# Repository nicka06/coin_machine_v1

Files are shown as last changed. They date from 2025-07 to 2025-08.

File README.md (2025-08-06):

# coin_machine_v1

This is an automated coin machine, allowing an individual to easily take pictures of all the coins that they have. It works very simply. The user inserts the coin into the chute located at the front of the machine. Once the coin has made its way to the flipper, the servo flips it over twice, allowing the camera to take a picture of both sides. Following the completion of the flips, the coin is ejected, taking it through external coin chute and collection box. Beyond the mechanics of the camera/flipper system, the system has an additional chute that is opened by the servo connected to the excursion on the right side of the mahine. If the system recognizes multiple coins in the system (via the phototransistor sensor), the chute will open up, removing the extra coins from the system via the second external coin chute. This coin chute brings the extra coins to the front of the machine.

I'm building this automated coin machine due to my love of coins. I enjoy collecting them and taking pictures of the new ones I get at the bank to keep track of them. As you can imagine, this is an extremely difficult and annoying process. This cuts through all of it, making the grueling process much better. Later, I'll also be able to add more features such as automatic value estimator and more. I can't wait to finish building it!
Screenshot 2025-08-06 at 12 46 12 AM
Front chute
Screenshot 2025-08-06 at 12 53 51 AM

Screenshot 2025-07-26 at 3 54 14 PM

|Item |Link |Step/STL File |Price (bf tax + ship)|Quantity|Total |
|---|---|---|---|---|---|
|Microcontroller |https://www.digikey.com/en/products/detail/espressif-systems/ESP32-DEVKITC-32E/12091810?gQT=2 |N/A |8.09 |1 |16.18 |
|Battery Holder |https://www.digikey.com/en/products/detail/olimex-ltd/BAT-HOLDER-4XAA/21662650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 |DNE |0.59 |1 |1.18  |
|Servos |https://www.amazon.com/Miuzei-Geared-Helicopter-Arduino-Project/dp/B0CP98TZJ2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 |https://www.electronicoscaldas.com/datasheet/MG90S_Tower-Pro.pdf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 |13.99 |0.5 |13.99 |
|Sensor |https://www.digikey.com/en/products/detail/lite-on-inc/LTH-301-05/3198344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 |https://optoelectronics.liteon.com/upload/download/DS-55-92-0002/H301-05.pdf |0.7 |1 |1.4 |
|Light indicator |https://www.digikey.com/en/products/detail/inolux/HV-5RGB60/7604616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 |https://www.inolux-corp.com/datasheet/Inolux%20Lamp/TH%20Lamp/HV-5RGBXX%205mm%20Full-Color%20Series.pdf |1.06 |1 |2.12  |
|Camera |https://www.alibaba.com/product-detail/p_62408774762.html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 |https://us-icbuim-file.oss-us-east-1.aliyuncs.com/chat/bdf5eb8cdbcff22f275396a9d335c13d.pdf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|1.92 |1 |3.84  |
|Camera lights |https://www.amazon.com/BTF-LIGHTING-WS2812B1M60LB30-BTF-LIGHTING-WS2812B-IC-RGB-5050SMD-Pure-Gold-Individual-Addressable-LED-Strip-High-Quality-3-28FT-60LED-60LED-m-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 |DNE |8.99 |0.5 |8.99  |
|buck converter |https://www.alibaba.com/product-detail/p_1601286665356.html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 |DNE |0.38 |1 |0.76  |
|1000Uf Capacitor |https://www.digikey.com/en/products/detail/nichicon/UCM1C102MNL1GS/4991837 |N/A |1.03 |1 |2.06  |
|indicator resistor  |https://www.digikey.com/en/products/detail/yageo/RC0805FR-10220RL/14008826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 |N/A |0.1 |1 |0.2 |
|ligihting resistor  |https://www.digikey.com/en/products/detail/yageo/RC0805FR-13470RL/14287677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 |N/A |0.1 |3 |0.6 |
|Power Connector |https://www.digikey.com/en/products/detail/w-rth-elektronik/691137710002/6644051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 |N/A |0.74 |1 |1.48  |
|Servo connector |https://www.digikey.com/en/products/detail/w-rth-elektronik/61300311121/4846825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 |N/A |0.12 |2 |0.48  |
|Sensor board male |https://www.digikey.com/en/products/detail/jst-sales-america-inc/B4B-XH-A/1651047 |N/A |0.14 |1 |0.28  |
|Sensor female |https://www.digikey.com/en/products/detail/jst-sales-america-inc/XHP-4/683353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 |N/A |0.1 |1 |0.2 |
|Sensor Connector |https://www.digikey.com/en/products/detail/jst-sales-america-inc/ASXHSXH22K254/9961919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 |N/A |0.77 |4 |6.16  |
|Indicator board male|https://www.digikey.com/en/products/detail/jst-sales-america-inc/B4B-XH-A/1651047 |N/A |0.14 |1 |0.28  |
|Indicator Female |https://www.digikey.com/en/products/detail/jst-sales-america-inc/XHP-4/683353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 |N/A |0.1 |1 |0.2 |
|Indicator Connector |https://www.digikey.com/en/products/detail/jst-sales-america-inc/ASXHSXH22K254/9961919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 |N/A |0.77 |4 |6.16  |
|Lightning Board Male|https://www.digikey.com/en/products/detail/jst-sales-america-inc/B3B-XH-A/1651046?gQT=2 |N/A |0.11 |1 |0.22  |
|Lightning Female |https://www.digikey.com/en/products/detail/jst-sales-america-inc/XHP-3/1651017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 |N/A |0.1 |1 |0.2 |
|Lightning Connector |https://www.digikey.com/en/products/detail/jst-sales-america-inc/ASXHSXH22K102/9961917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 |N/A |0.71 |3 |4.26  |
|Camera Connector |https://www.digikey.com/en/products/detail/gct/FFC2B35-24-T/15970899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 |N/A |0.44 |1 |0.88  |
|Camera Wire |https://www.digikey.com/en/products/detail/gct/05-24-D-0101-A-4-06-4-T/21266768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 |N/A |1.29 |1 |2.58  |
|Regular wire |https://www.amazon.com/Fermerry-Stranded-Electrical-Silicone-Cables/dp/B089CHVN7G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 |N/A |9.99 |0.5 |9.99  |
|Foam for pcb |https://www.aliexpress.us/item/3256805442378894.html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 |N/A |6.58 |0.5 |6.58  |
|Screws |https://www.homedepot.com/p/Everbilt-M3-0-5-x-10-mm-Plain-Metric-Socket-Cap-Screw-3-Piece-per-Bag-803188/204808024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 |N/A |2.25 |2 |9 |
|More Screws |https://www.homedepot.com/p/Prime-Line-M2-0-4-x-20-mm-Black-Oxide-Coated-Steel-Class-12-9-Metric-Internal-Hex-Socket-Head-Set-Screws-10-Pack-9180136/311732337 |N/A |4.99 |0.5 |4.99  |
|Magnets |https://www.aliexpress.us/item/3256807909032358.html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|N/A |0.99 |1 |1.98  |
|filament |https://www.amazon.com/eSUN-Filament-Printing-Printer-Designed/dp/B0DGQBMJMK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 |N/A |13.39 |0.5 |13.39 |
|pcb |N/A |N/A |2 |0.5 |2 |
|Shipping + Tax | | | | |35 |
| | | | | |157.63|
| | |a | | | |

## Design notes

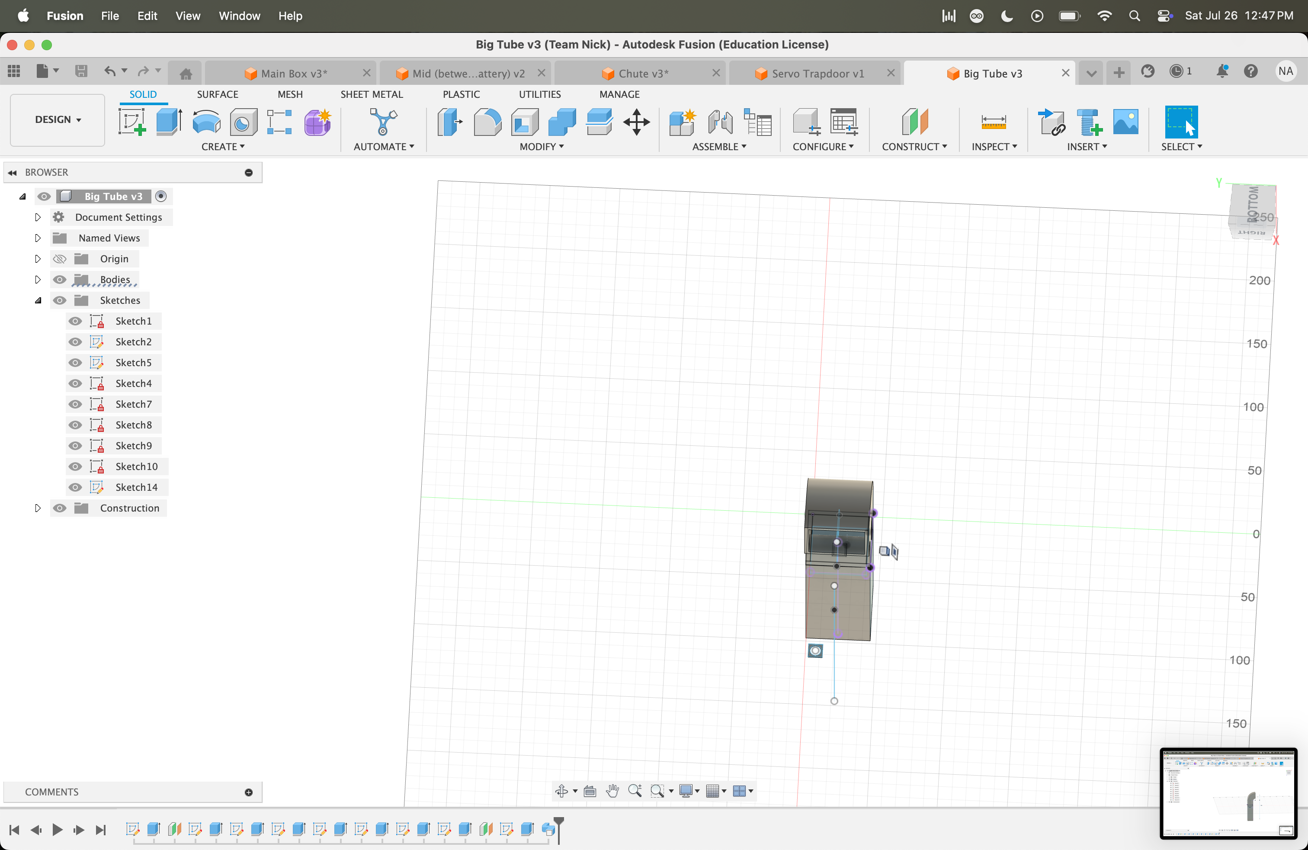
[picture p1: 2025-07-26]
pics/Screenshot 2025-07-26 at 12.47.22 PM.png

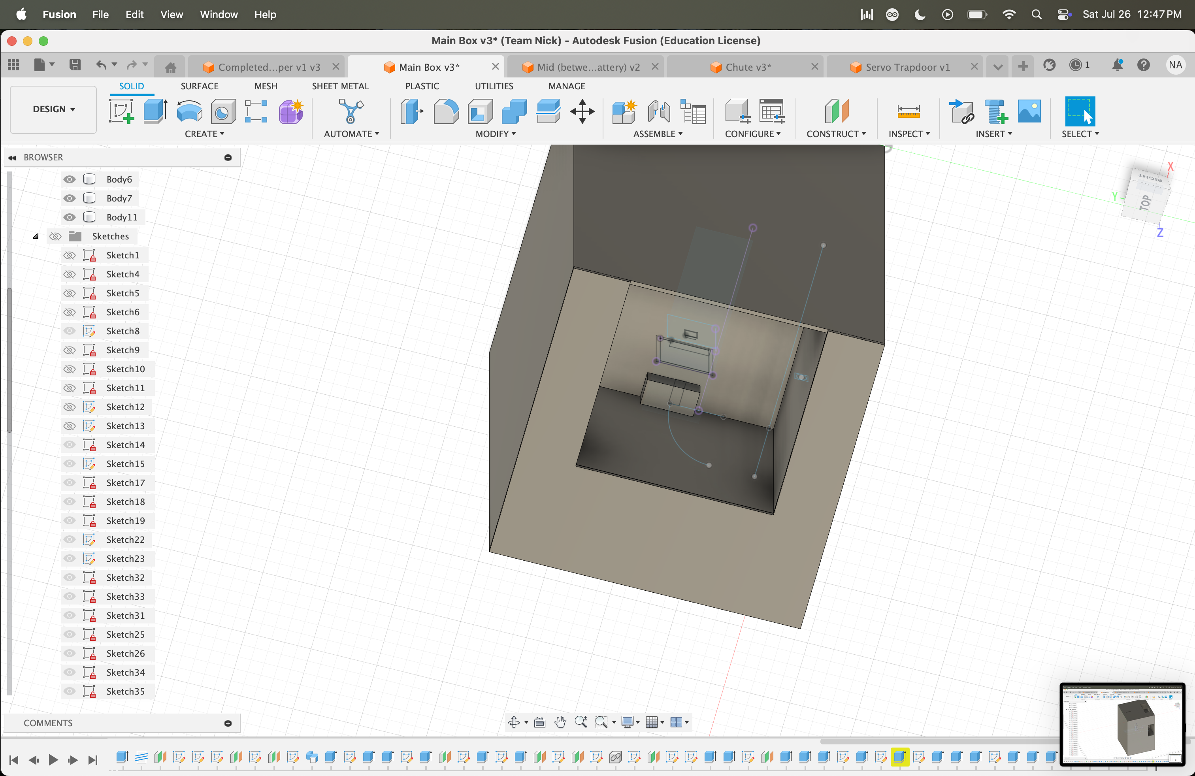
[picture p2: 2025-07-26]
pics/Screenshot 2025-07-26 at 12.47.51 PM.png

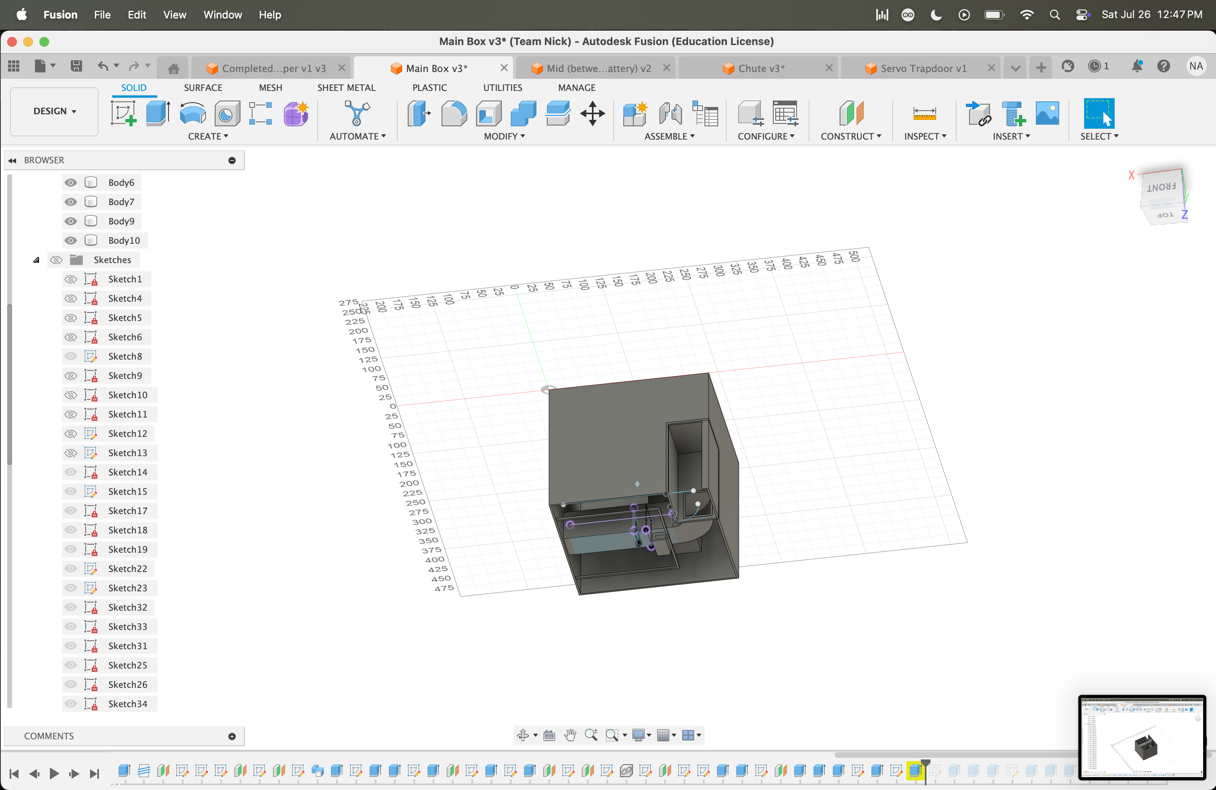
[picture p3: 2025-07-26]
pics/Screenshot 2025-07-26 at 12.47.39 PM.png

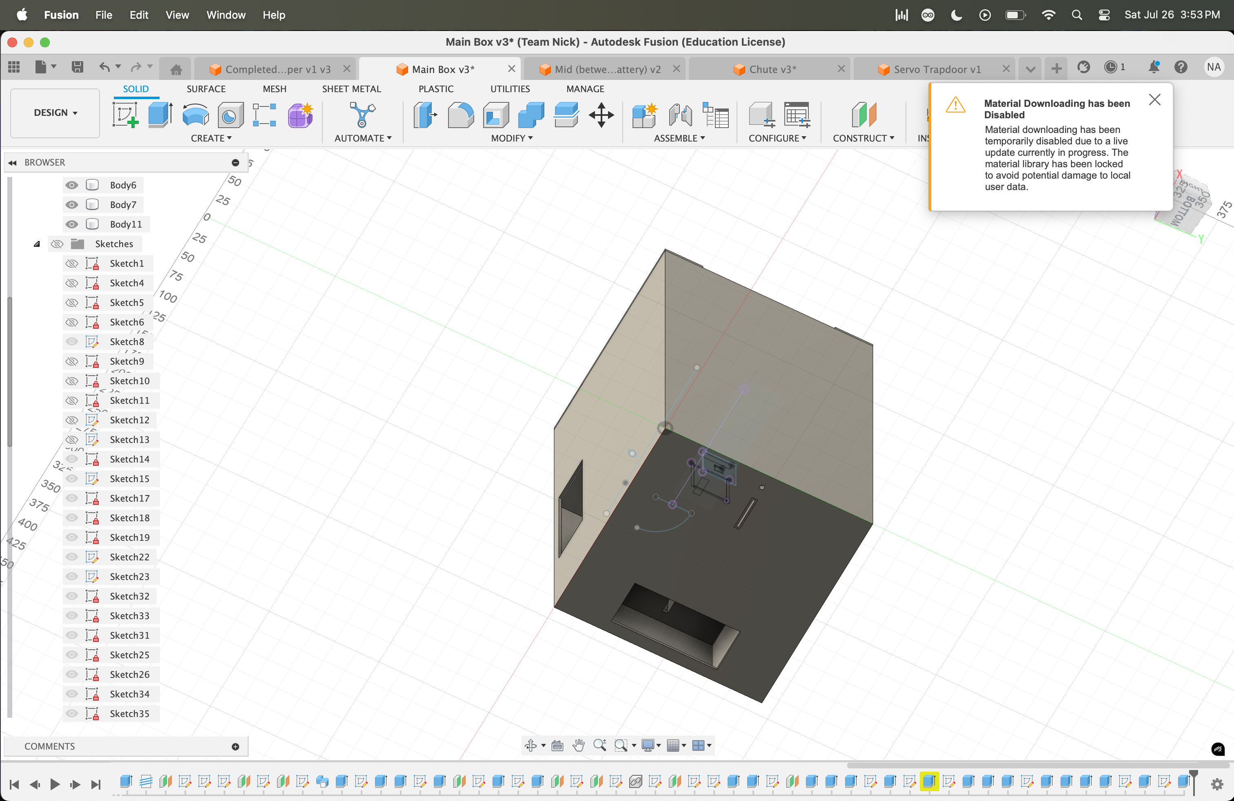
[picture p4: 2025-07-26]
pics/Screenshot 2025-07-26 at 3.53.41 PM.png

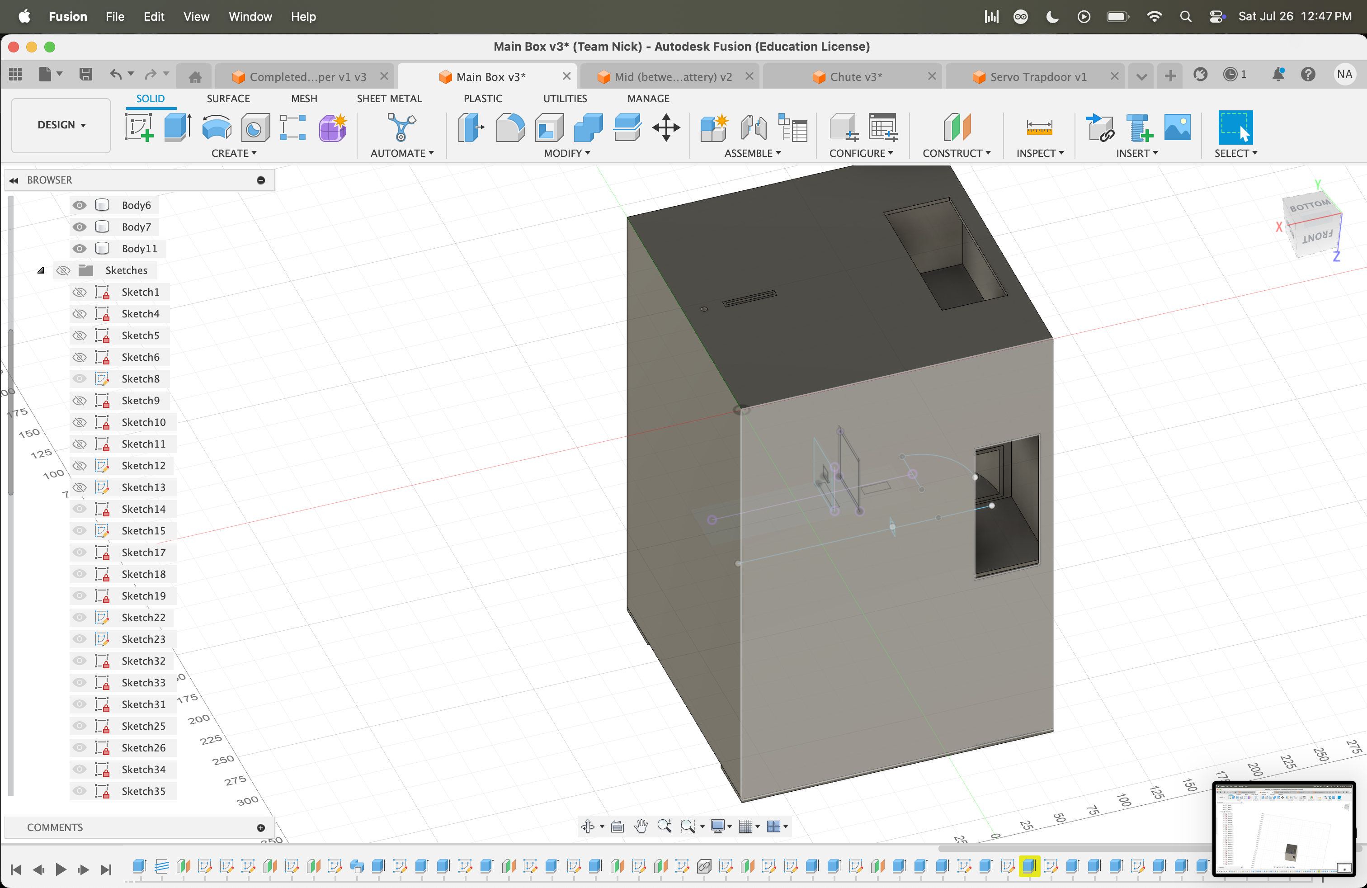
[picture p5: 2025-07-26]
pics/Screenshot 2025-07-26 at 12.47.49 PM.png

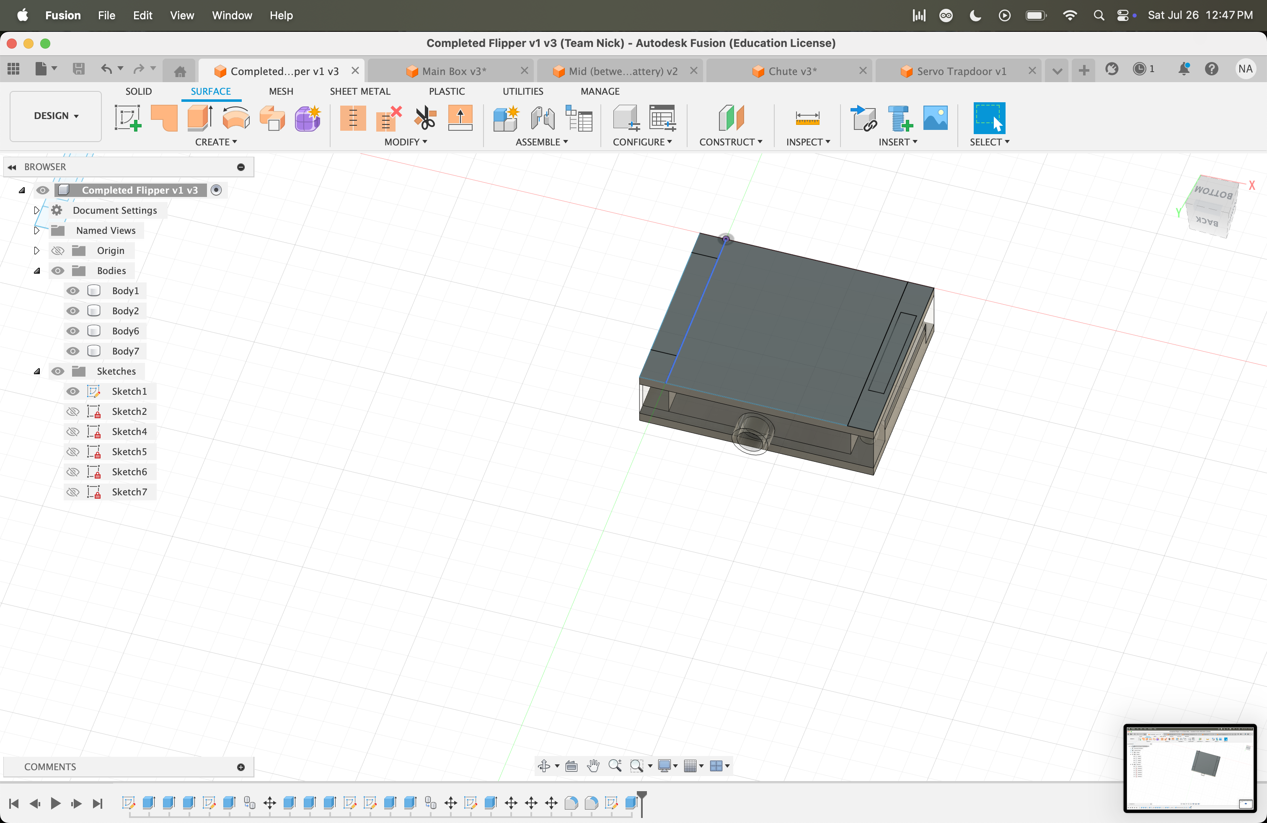
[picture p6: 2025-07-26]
pics/Screenshot 2025-07-26 at 12.47.08 PM.png

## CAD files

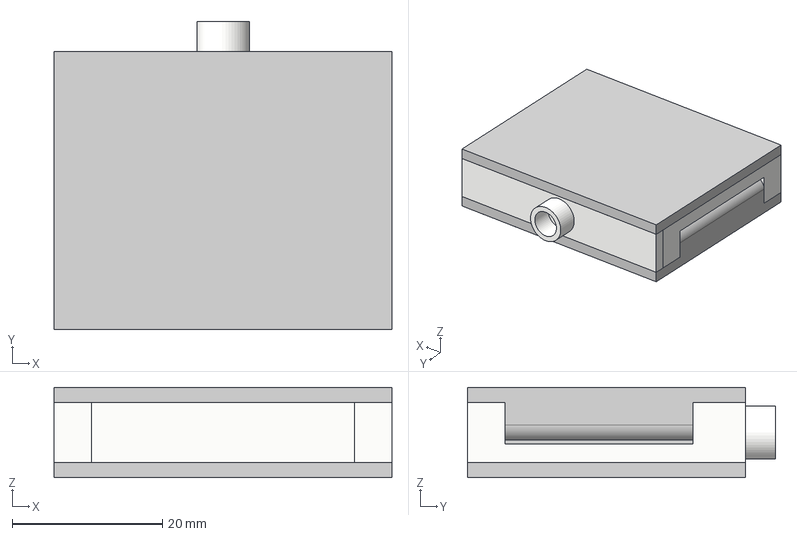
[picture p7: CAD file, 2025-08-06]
cad/Completed Flipper v1 v3.step
45.0 x 41.0 x 12.0 mm

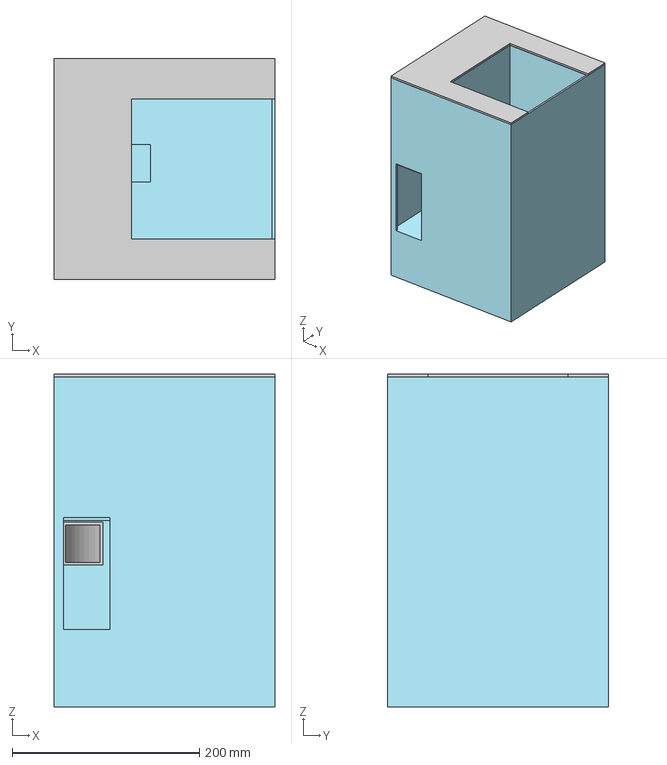
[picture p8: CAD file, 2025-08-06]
cad/Main Box v6.step
236.2 x 236.2 x 356.0 mm
Big Tube
Chute

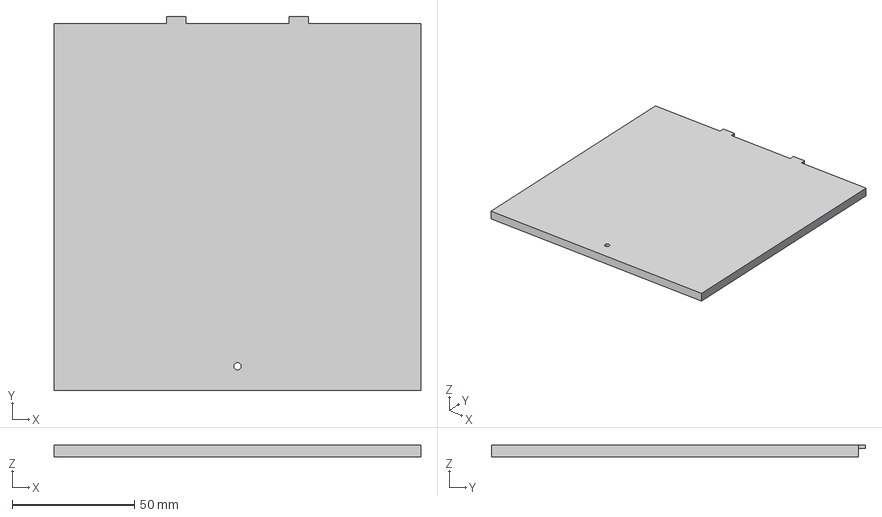
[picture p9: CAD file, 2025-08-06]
cad/Back Side v2.step
150.0 x 153.0 x 5.00 mm

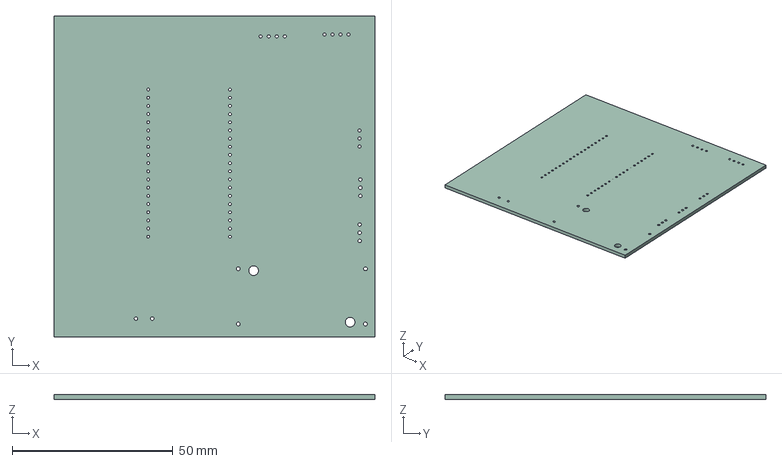
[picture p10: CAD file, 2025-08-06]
cad/Automated Coin Machine v1.step
99.6 x 99.7 x 1.51 mm

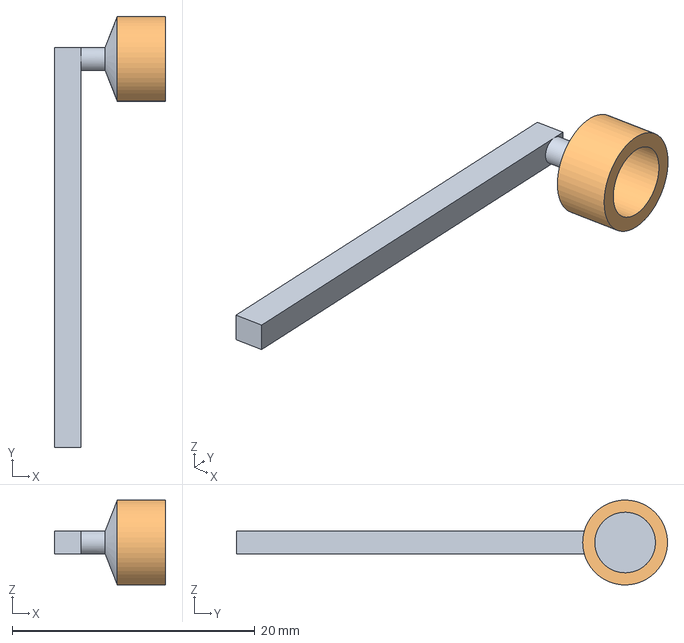
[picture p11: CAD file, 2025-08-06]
cad/Servo Trapdoor v1.step
9.19 x 35.5 x 7.00 mm

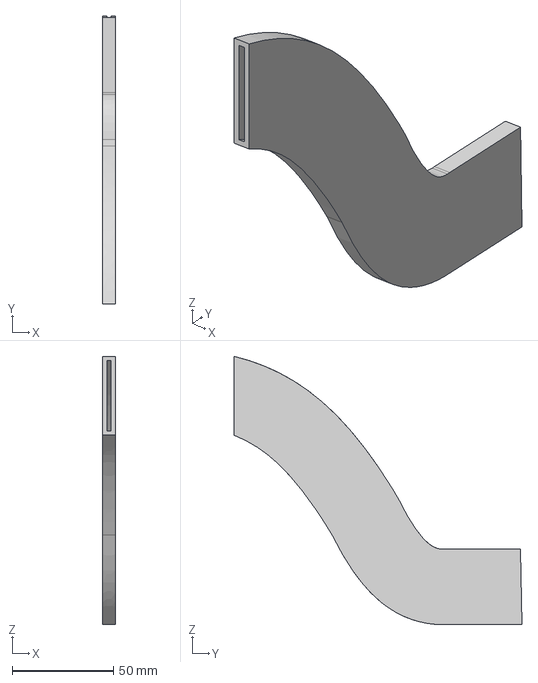
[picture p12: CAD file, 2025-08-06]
cad/Chute v4.step
6.20 x 142.4 x 132.6 mm

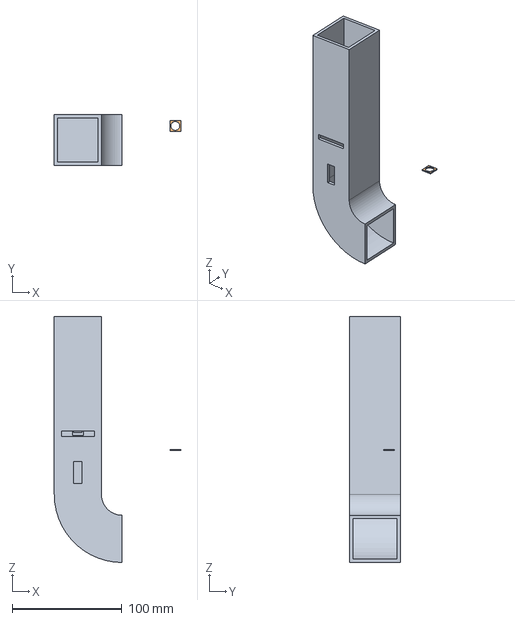
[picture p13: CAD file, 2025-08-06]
cad/Big Tube v3.step
115.2 x 46.0 x 224.0 mm

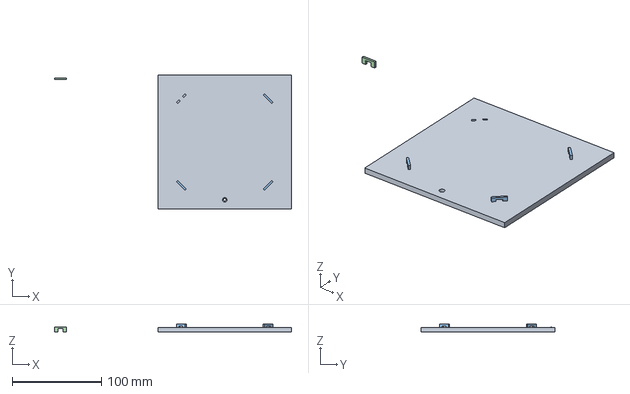
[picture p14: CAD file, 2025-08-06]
cad/PCB Plate v2.step
266.3 x 150.0 x 8.80 mm

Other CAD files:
cad/Main Box v4.stl
cad/Mid (between pcb and battery) v2.step
cad/Back Side v2.stl
cad/Big Tube v3.stl
cad/Chute v4.stl
cad/Completed Flipper v1 v3.stl
cad/Mid (between pcb and battery) v2.stl
cad/PCB Plate v2.stl
cad/Servo Trapdoor v1.stl

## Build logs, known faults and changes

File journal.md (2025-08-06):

---
title: Automated Coin Machine
author: Nick
description: Automates Coin Recognition
created_at: "2024-07-20"
---

Total Time Spent ~ 20 hrs

7/20/2025 -- 1.5 hours

Forgot to update this yesterday but I'll go ahead and do this now. I started to work on the cad for the actual flipper that will open up and allow the coins to take the images. It essentially works by having two magnets that hold it shut when it's not being pried open by the bar in the main rectangular tube. These act as the bottoms so the coin doens't fall down the chute prematurely. The actual "cading" wasn't too hard but I had to go back several times to make adjustments on the sizing. I also sketched out the rest of the box and started to create a bom. I'll attach an image of the sketches that I made yesterday


7/21/2025 --3 hours

Continued to build out the chute on the cad as well as the bom. The bill of materials has been harder than I originally thought as finding the correct parts and then making sure that the schematic and 3d orientation will work correctly all togethor is nothing short of a pain in the butt. Additionally, when building out the chute, I couldn't figure out how to get it to go along on the path that I wanted it to go on. I looked it up on chat gpt, google, reddit, etc and nothing worked. Eventually, I just created it using the sweep and then extruded a cut so that the one end would be flat 90 degrees but there has to be a better way of going about that. 
Screenshot 2025-07-22 at 11 32 43 PM
Screenshot 2025-07-22 at 11 33 04 PM

7/22/2025 -4 hours

Created all of the symbols and built out the schematic. This was a HUGE pain in the butt, but kinda fun at the same time. The good news is that it sort of paid off to go through all the bill of materials was correct the first time. I had to consult with chat gpt and google a lot when building out most of the schematic as I'm fairly novice in this work. In terms of efficiency, I feel like 4-5 hours for working on a schematic isn't that bad especially for someone who hasn't done it a ton like me. 

Screenshot 2025-07-22 at 11 34 23 PM

Screenshot 2025-07-23 at 1 27 12 PM
Screenshot 2025-07-23 at 1 27 17 PM

7/24/2025 - 5 hrs

Started to build out the actual box and rest of the components via fusion360 to finish up the project. This should have gone a lot easier then it did. Despite the fact that I had all the pieces with the correct heights and dimensions on them, the pieces were still really finnecky when going into place. Eventually, I looked up a manual for fusion 3690 and realized that you can do point to point connections which turned out to be a life saver. Will finish the rest of the cad by tomorrow. 

7/25/2025 - 1 HR

Again, I continue to work on the project. Today, I had a huge setback as I realized the chute ran into the servo. WHAT A PAIN. So, I took some time to extrude another 3.6 millimaters to the end of the chute and then extended the rest of the infastructure (flipper, main rectangular thing, side exterior coin holder, etc) so that all of that would work with the new dimensions that i worked with.
7/26/2025 - 4 hrs

Finished everyhting up!!! The final github uploads and downloading all the content wasn't a whole lot of fund but Ican feel how ready I am to start building it out!

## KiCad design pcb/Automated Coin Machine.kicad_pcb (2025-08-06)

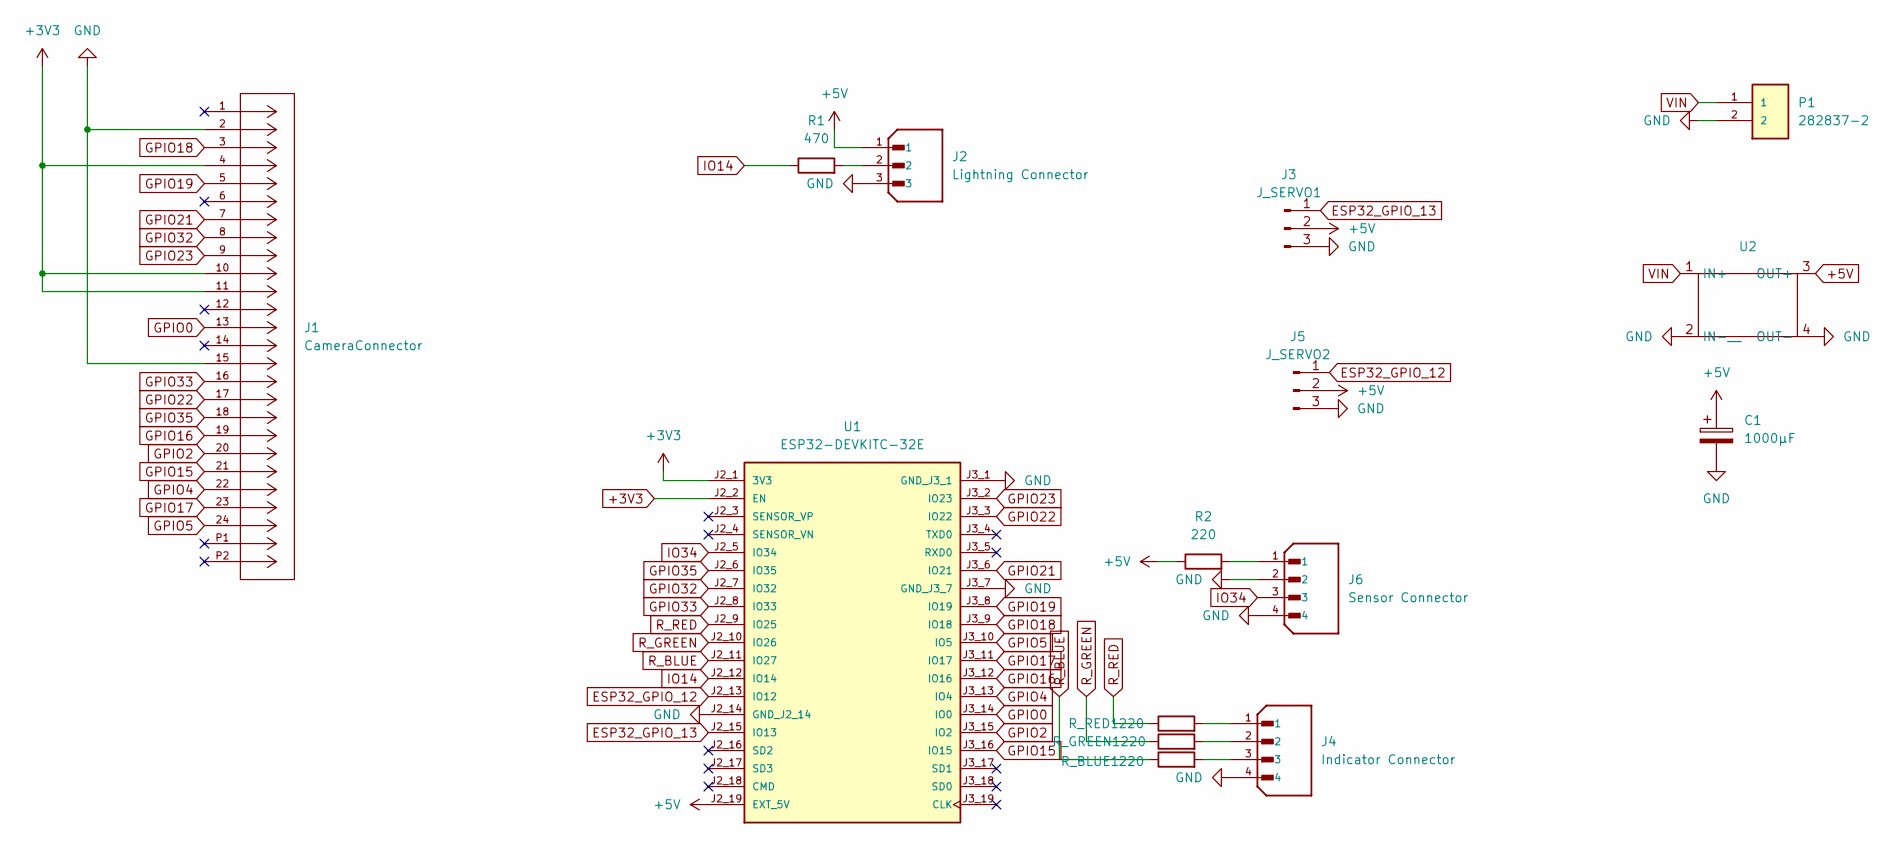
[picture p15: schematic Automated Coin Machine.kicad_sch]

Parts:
C1: 1000µF; 1000UFCapacitor
J1: CameraConnector; MANUFACTURER_PART_NUMBER 5051102491
J2: Lightning Connector; LightningConnector; PARTREV 7/4/21; DigiKey_Part_Number 455-2248-ND
J3: J_SERVO1; ServoConnector
J4: Indicator Connector; SensorIndicatorConnector; PARTREV 7/4/21; DigiKey_Part_Number 455-B4B-XH-A-ND
J5: J_SERVO2; ServoConnector
J6: Sensor Connector; SensorIndicatorConnector; PARTREV 7/4/21; DigiKey_Part_Number 455-B4B-XH-A-ND
P1: 282837-2; PowerConnector; PARTREV G3
R1: 470; LightningResistor
R2: 220; IndicatorResistor
R_BLUE1: 220; IndicatorResistor
R_GREEN1: 220; IndicatorResistor
R_RED1: 220; IndicatorResistor
U1: ESP32-DEVKITC-32E; ESP32; PARTREV 1.4
U2: LM2596_Module

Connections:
+3V3: J1.4, J1.10, J1.11, U1.J2_1 (3V3), U1.J2_2 (EN)
+5V: C1.1, J2.1, J3.2, J5.2, R2.1, U1.J2_19 (EXT_5V), U2.3 (OUT+)
ESP32_GPIO_12: J5.1, U1.J2_13 (IO12)
ESP32_GPIO_13: J3.1, U1.J2_15 (IO13)
GND: C1.2, J1.2, J1.15, J2.3, J3.3, J4.4, J5.3, J6.2, J6.4, P1.2, U1.J2_14 (GND_J2_14), U1.J3_1 (GND_J3_1), U1.J3_7 (GND_J3_7), U2.2 (IN-__), U2.4 (OUT-)
GPIO0: J1.13, U1.J3_14 (IO0)
GPIO2: J1.20, U1.J3_15 (IO2)
GPIO4: J1.22, U1.J3_13 (IO4)
GPIO5: J1.24, U1.J3_10 (IO5)
GPIO15: J1.21, U1.J3_16 (IO15)
GPIO16: J1.19, U1.J3_12 (IO16)
GPIO17: J1.23, U1.J3_11 (IO17)
GPIO18: J1.3, U1.J3_9 (IO18)
GPIO19: J1.5, U1.J3_8 (IO19)
GPIO21: J1.7, U1.J3_6 (IO21)
GPIO22: J1.17, U1.J3_3 (IO22)
GPIO23: J1.9, U1.J3_2 (IO23)
GPIO32: J1.8, U1.J2_7 (IO32)
GPIO33: J1.16, U1.J2_8 (IO33)
GPIO35: J1.18, U1.J2_6 (IO35)
IO14: R1.1, U1.J2_12 (IO14)
IO34: J6.3, U1.J2_5 (IO34)
unnamed: J2.2, R1.2
unnamed: J4.1, R_RED1.2
unnamed: J4.2, R_GREEN1.2
unnamed: J4.3, R_BLUE1.2
unnamed: J6.1, R2.2
R_BLUE: R_BLUE1.1, U1.J2_11 (IO27)
R_GREEN: R_GREEN1.1, U1.J2_10 (IO26)
R_RED: R_RED1.1, U1.J2_9 (IO25)
VIN: P1.1, U2.1 (IN+)

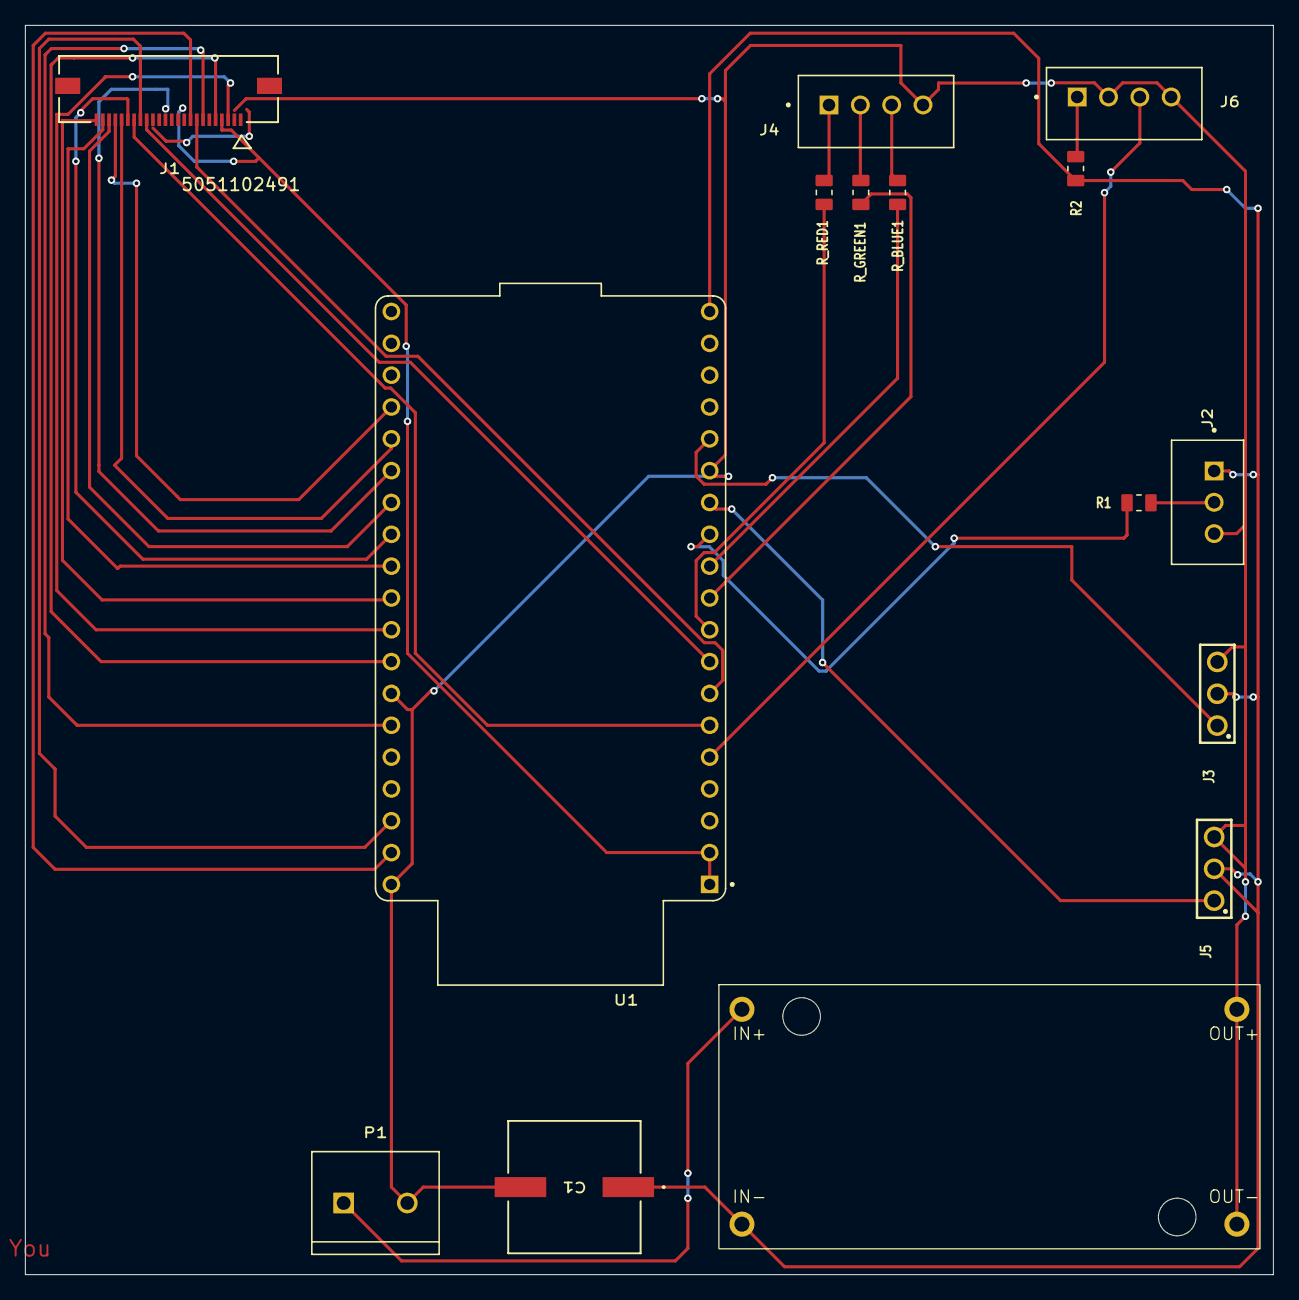
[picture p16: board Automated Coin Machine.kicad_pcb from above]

Board: 2 copper layers, 99.6 x 99.7 mm, 15 parts (0 on the bottom side), 31 nets.

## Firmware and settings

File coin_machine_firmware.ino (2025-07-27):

/*
 * Automated Coin Machine Firmware
 * ESP32 Arduino Code
 * 
 * This firmware controls an automated coin recognition system with:
 * - Optical sensor for coin detection
 * - Servo-controlled trapdoor for rejecting multiple coins
 * - Servo-controlled flipper for coin positioning
 * - OV2640 camera for coin photography
 * - WS2812B LED lighting for photography
 * - RGB status indicator
 */

#include "config.h"
#include "hardware_functions.h"

// ==================== GLOBAL VARIABLES ====================
// Hardware objects
Servo trapdoorServo;
Servo flipperServo;
CRGB cameraLEDs[NUM_CAMERA_LEDS];

// State machine variables
CoinMachineState currentState = STATE_INIT;
CoinMachineState previousState = STATE_INIT;
unsigned long stateStartTime = 0;
unsigned long lastStateTime = 0;

// Timing variables
unsigned long trapdoorOpenTime = 0;
unsigned long flipperMoveTime = 0;
unsigned long photographSequenceTime = 0;

// Processing variables
bool processingCoin = false;
int currentPhotoStep = 0;
String currentImageFilename1 = "";
String currentImageFilename2 = "";

// Error handling
StatusCode lastError = STATUS_OK;
int errorCount = 0;

// ==================== SETUP FUNCTION ====================
void setup() {
    Serial.begin(SERIAL_BAUD_RATE);
    delay(1000);
    
    DEBUG_PRINTLN("=== Automated Coin Machine Starting ===");
    DEBUG_PRINTLN("Initializing hardware...");
    
    // Initialize all hardware components
    bool initSuccess = true;
    
    if (!initializeStorage()) {
        DEBUG_PRINTLN("ERROR: Storage initialization failed");
        initSuccess = false;
    }
    
    if (!initializeCamera()) {
        DEBUG_PRINTLN("ERROR: Camera initialization failed");
        initSuccess = false;
    }
    
    if (!initializeServos()) {
        DEBUG_PRINTLN("ERROR: Servo initialization failed");
        initSuccess = false;
    }
    
    if (!initializeLEDs()) {
        DEBUG_PRINTLN("ERROR: LED initialization failed");
        initSuccess = false;
    }
    
    if (!initializeSensor()) {
        DEBUG_PRINTLN("ERROR: Sensor initialization failed");
        initSuccess = false;
    }
    
    // Check initialization results
    if (!initSuccess) {
        currentState = STATE_ERROR;
        setStatusLED(LED_ERROR);
        DEBUG_PRINTLN("FATAL: Hardware initialization failed");
        return;
    }
    
    // Perform system test
    DEBUG_PRINTLN("Performing system test...");
    performSystemTest();
    
    // Clean up old images
    cleanupOldImages();
    
    // Initialize state machine
    changeState(STATE_WAITING_FOR_COIN);
    
    DEBUG_PRINTLN("=== System Ready ===");
    DEBUG_PRINTLN("Waiting for coins...");
}

// ==================== MAIN LOOP ====================
void loop() {
    unsigned long currentTime = millis();
    
    // Update state timing
    unsigned long timeInState = currentTime - stateStartTime;
    
    // Handle timeout protection
    if (timeInState > RESET_TIMEOUT) {
        DEBUG_PRINTLN("WARNING: State timeout, performing reset");
        handleError(STATUS_TIMEOUT_ERROR);
        return;
    }
    
    // State machine dispatcher
    switch (currentState) {
        case STATE_INIT:
            // Should not reach here after setup
            changeState(STATE_WAITING_FOR_COIN);
            break;
            
        case STATE_WAITING_FOR_COIN:
            handleWaitingForCoin();
            break;
            
        case STATE_COIN_DETECTED:
            handleCoinDetected();
            break;
            
        case STATE_PROCESSING:
            handleProcessing();
            break;
            
        case STATE_PHOTOGRAPHING:
            handlePhotographing();
            break;
            
        case STATE_REJECTING:
            handleRejecting();
            break;
            
        case STATE_ERROR:
            handleError(lastError);
            break;
            
        default:
            DEBUG_PRINTLN("ERROR: Unknown state");
            changeState(STATE_ERROR);
            break;
    }
    
    // Process serial commands for debugging
    processSerialCommands();
    
    // Small delay to prevent excessive CPU usage
    delay(10);
}

// ==================== STATE HANDLERS ====================

void handleWaitingForCoin() {
    // Set ready status
    setStatusLED(LED_READY);
    
    // Check for sensor trigger
    if (isSensorTriggered()) {
        DEBUG_PRINTLN("Coin detected!");
        changeState(STATE_COIN_DETECTED);
        clearSensorTrigger();
    }
}

void handleCoinDetected() {
    setStatusLED(LED_PROCESSING);
    
    unsigned long timeInState = millis() - stateStartTime;
    
    // Wait for the detection window to complete
    if (timeInState >= MULTI_COIN_TIMEOUT) {
        // Check if multiple coins were detected
        if (isMultipleCoinDetected()) {
            DEBUG_PRINTLN("Multiple coins detected - rejecting");
            changeState(STATE_REJECTING);
            lastError = STATUS_MULTIPLE_COINS;
        } else {
            DEBUG_PRINTLN("Single coin detected - processing");
            changeState(STATE_PROCESSING);
        }
        resetSensorCount();
    }
}

void handleProcessing() {
    setStatusLED(LED_PROCESSING);
    
    // Check for additional coins during processing
    if (isSensorTriggered()) {
        DEBUG_PRINTLN("Additional coin detected during processing - rejecting");
        clearSensorTrigger();
        resetSensorCount();
        changeState(STATE_REJECTING);
        lastError = STATUS_COIN_DURING_PROCESSING;
        return;
    }
    
    unsigned long timeInState = millis() - stateStartTime;
    
    // Brief settling time before starting photography
    if (timeInState >= 500) {
        DEBUG_PRINTLN("Starting photography sequence");
        changeState(STATE_PHOTOGRAPHING);
        currentPhotoStep = 0;
    }
}

void handlePhotographing() {
    setStatusLED(LED_BUSY);
    
    unsigned long timeInState = millis() - stateStartTime;
    
    switch (currentPhotoStep) {
        case 0: // Move flipper to first position (90 degrees)
            DEBUG_PRINTLN("Moving flipper to first position");
            moveFlipperToSide1();
            flipperMoveTime = millis();
            currentPhotoStep = 1;
            break;
            
        case 1: // Wait for flipper to reach position, then take first photo
            if (millis() - flipperMoveTime >= SERVO_MOVE_DELAY) {
                DEBUG_PRINTLN("Taking first photo");
                currentImageFilename1 = generateImageFilename();
                
                if (captureAndSaveImage(currentImageFilename1.c_str())) {
                    DEBUG_PRINTLN("First photo captured successfully");
                    currentPhotoStep = 2;
                    flipperMoveTime = millis();
                } else {
                    DEBUG_PRINTLN("ERROR: First photo capture failed");
                    handleError(STATUS_CAMERA_ERROR);
                    return;
                }
            }
            break;
            
        case 2: // Move flipper to second position (180 degrees)
            if (millis() - flipperMoveTime >= FLIPPER_PHOTO_DELAY) {
                DEBUG_PRINTLN("Moving flipper to second position");
                moveFlipperToSide2();
                flipperMoveTime = millis();
                currentPhotoStep = 3;
            }
            break;
            
        case 3: // Wait for flipper to reach position, then take second photo
            if (millis() - flipperMoveTime >= SERVO_MOVE_DELAY) {
                DEBUG_PRINTLN("Taking second photo");
                currentImageFilename2 = generateImageFilename();
                
                if (captureAndSaveImage(currentImageFilename2.c_str())) {
                    DEBUG_PRINTLN("Second photo captured successfully");
                    currentPhotoStep = 4;
                    flipperMoveTime = millis();
                } else {
                    DEBUG_PRINTLN("ERROR: Second photo capture failed");
                    handleError(STATUS_CAMERA_ERROR);
                    return;
                }
            }
            break;
            
        case 4: // Return flipper to home position
            if (millis() - flipperMoveTime >= FLIPPER_PHOTO_DELAY) {
                DEBUG_PRINTLN("Returning flipper to home position");
                moveFlipperHome();
                flipperMoveTime = millis();
                currentPhotoStep = 5;
            }
            break;
            
        case 5: // Wait for flipper to reach home, then complete
            if (millis() - flipperMoveTime >= SERVO_MOVE_DELAY) {
                DEBUG_PRINTLN("Photography sequence complete");
                DEBUG_PRINT("Images saved: ");
                DEBUG_PRINT(currentImageFilename1);
                DEBUG_PRINT(", ");
                DEBUG_PRINTLN(currentImageFilename2);
                
                // Reset for next coin
                currentPhotoStep = 0;
                changeState(STATE_WAITING_FOR_COIN);
            }
            break;
    }
    
    // Timeout protection for photography sequence
    if (timeInState > PROCESSING_TIMEOUT) {
        DEBUG_PRINTLN("ERROR: Photography sequence timeout");
        handleError(STATUS_TIMEOUT_ERROR);
    }
}

void handleRejecting() {
    setStatusLED(LED_ERROR);
    
    unsigned long timeInState = millis() - stateStartTime;
    
    // Open trapdoor immediately when entering rejection state
    if (timeInState < 100) {
        DEBUG_PRINTLN("Opening rejection trapdoor");
        openTrapdoor();
        trapdoorOpenTime = millis();
    }
    
    // Close trapdoor after specified time
    if (timeInState >= TRAPDOOR_OPEN_TIME) {
        DEBUG_PRINTLN("Closing rejection trapdoor");
        closeTrapdoor();
        
        // Wait a bit more for trapdoor to close, then return to waiting
        if (timeInState >= TRAPDOOR_OPEN_TIME + 1000) {
            DEBUG_PRINTLN("Rejection complete, ready for next coin");
            changeState(STATE_WAITING_FOR_COIN);
        }
    }
}

void handleError(StatusCode error) {
    setStatusLED(LED_ERROR);
    
    static unsigned long lastErrorReport = 0;
    unsigned long currentTime = millis();
    
    // Report error periodically
    if (currentTime - lastErrorReport > 5000) {
        DEBUG_PRINT("ERROR STATE: ");
        switch (error) {
            case STATUS_MULTIPLE_COINS:
                DEBUG_PRINTLN("Multiple coins detected");
                break;
            case STATUS_COIN_DURING_PROCESSING:
                DEBUG_PRINTLN("Coin detected during processing");
                break;
            case STATUS_CAMERA_ERROR:
                DEBUG_PRINTLN("Camera error");
                break;
            case STATUS_STORAGE_ERROR:
                DEBUG_PRINTLN("Storage error");
                break;
            case STATUS_TIMEOUT_ERROR:
                DEBUG_PRINTLN("Timeout error");
                break;
            default:
                DEBUG_PRINTLN("Unknown error");
                break;
        }
        lastErrorReport = currentTime;
        errorCount++;
    }
    
    // Auto-recovery after multiple error reports
    if (errorCount >= 3) {
        DEBUG_PRINTLN("Attempting system recovery...");
        systemReset();
        errorCount = 0;
        changeState(STATE_WAITING_FOR_COIN);
    }
}

// ==================== UTILITY FUNCTIONS ====================

void changeState(CoinMachineState newState) {
    if (newState != currentState) {
        previousState = currentState;
        currentState = newState;
        stateStartTime = millis();
        
        DEBUG_PRINT("State change: ");
        DEBUG_PRINT(getStateName(previousState));
        DEBUG_PRINT(" -> ");
        DEBUG_PRINTLN(getStateName(currentState));
        
        // Reset variables when changing states
        if (newState == STATE_WAITING_FOR_COIN) {
            processingCoin = false;
            resetSensorCount();
            lastError = STATUS_OK;
        }
    }
}

const char* getStateName(CoinMachineState state) {
    switch (state) {
        case STATE_INIT: return "INIT";
        case STATE_WAITING_FOR_COIN: return "WAITING_FOR_COIN";
        case STATE_COIN_DETECTED: return "COIN_DETECTED";
        case STATE_PROCESSING: return "PROCESSING";
        case STATE_PHOTOGRAPHING: return "PHOTOGRAPHING";
        case STATE_REJECTING: return "REJECTING";
        case STATE_ERROR: return "ERROR";
        default: return "UNKNOWN";
    }
}

// ==================== INTERRUPT HANDLERS ====================
// Sensor interrupt handler is defined in hardware_functions.h

// ==================== DEBUG AND MONITORING ====================
void printSystemStatus() {
    DEBUG_PRINTLN("=== System Status ===");
    DEBUG_PRINT("Current State: ");
    DEBUG_PRINTLN(getStateName(currentState));
    DEBUG_PRINT("Time in State: ");
    DEBUG_PRINT(millis() - stateStartTime);
    DEBUG_PRINTLN("ms");
    DEBUG_PRINT("Sensor Trigger Count: ");
    DEBUG_PRINTLN(getSensorTriggerCount());
    DEBUG_PRINT("Error Count: ");
    DEBUG_PRINTLN(errorCount);
    DEBUG_PRINT("Free Heap: ");
    DEBUG_PRINTLN(ESP.getFreeHeap());
    DEBUG_PRINTLN("==================");
}

// Optional: Add serial command processing for debugging
void processSerialCommands() {
    if (Serial.available()) {
        String command = Serial.readStringUntil('\n');
        command.trim();
        
        if (command == "status") {
            printSystemStatus();
        } else if (command == "test") {
            performSystemTest();
        } else if (command == "reset") {
            systemReset();
            changeState(STATE_WAITING_FOR_COIN);
        } else if (command == "photos") {
            // List stored photos
            File root = SPIFFS.open("/");
            File file = root.openNextFile();
            DEBUG_PRINTLN("=== Stored Images ===");
            while (file) {
                if (String(file.name()).startsWith(IMAGE_FILENAME_PREFIX)) {
                    DEBUG_PRINT("- ");
                    DEBUG_PRINT(file.name());
                    DEBUG_PRINT(" (");
                    DEBUG_PRINT(file.size());
                    DEBUG_PRINTLN(" bytes)");
                }
                file = root.openNextFile();
            }
            DEBUG_PRINTLN("==================");
        } else {
            DEBUG_PRINTLN("Available commands: status, test, reset, photos");
        }
    }
} 

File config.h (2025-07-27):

#ifndef CONFIG_H
#define CONFIG_H

// ==================== PIN DEFINITIONS ====================
// Servo pins (avoiding camera pin conflicts)
#define TRAPDOOR_SERVO_PIN    16
#define FLIPPER_SERVO_PIN     17

// Sensor pins
#define OPTICAL_SENSOR_PIN    2   // Interrupt capable pin (changed from 21 to avoid I2C conflict)

// Camera pins (OV2640 - using default ESP32-CAM pins)
#define CAMERA_SDA_PIN        21
#define CAMERA_SCL_PIN        22
#define CAMERA_RESET_PIN      -1  // Not connected
#define CAMERA_XCLK_PIN       0
#define CAMERA_SIOD_PIN       26
#define CAMERA_SIOC_PIN       27
#define CAMERA_Y9_PIN         35
#define CAMERA_Y8_PIN         34
#define CAMERA_Y7_PIN         39
#define CAMERA_Y6_PIN         36
#define CAMERA_Y5_PIN         19
#define CAMERA_Y4_PIN         18
#define CAMERA_Y3_PIN         5
#define CAMERA_Y2_PIN         4
#define CAMERA_VSYNC_PIN      25
#define CAMERA_HREF_PIN       23
#define CAMERA_PCLK_PIN       22

// LED pins
#define STATUS_LED_R_PIN      12  // RGB status indicator
#define STATUS_LED_G_PIN      13
#define STATUS_LED_B_PIN      14
#define CAMERA_LIGHTS_PIN     15  // WS2812B strip data pin

// ==================== TIMING CONSTANTS ====================
// Servo timing (milliseconds)
#define TRAPDOOR_OPEN_TIME    2000    // How long trapdoor stays open
#define SERVO_MOVE_DELAY      500     // Delay between servo movements
#define FLIPPER_PHOTO_DELAY   300     // Delay after flipper moves before photo

// Sensor timing
#define SENSOR_DEBOUNCE_TIME  50      // Debounce delay for optical sensor
#define MULTI_COIN_TIMEOUT    1000    // Time window to detect multiple coins

// Camera timing
#define CAMERA_FLASH_DURATION 200     // LED flash duration during photo
#define CAMERA_WARMUP_TIME    100     // Camera stabilization time

// State timeouts
#define PROCESSING_TIMEOUT    10000   // Max time in processing state
#define RESET_TIMEOUT         30000   // Auto-reset if stuck

// ==================== SERVO POSITIONS ====================
// Trapdoor positions (degrees)
#define TRAPDOOR_CLOSED       0
#define TRAPDOOR_OPEN         90

// Flipper positions (degrees)
#define FLIPPER_HOME          0       // Starting position
#define FLIPPER_SIDE_1        90      // First photo position
#define FLIPPER_SIDE_2        180     // Second photo position (flipped)

// ==================== SENSOR THRESHOLDS ====================
#define MIN_COIN_BLOCK_TIME   10      // Minimum ms for valid coin detection
#define MAX_SINGLE_COIN_TIME  200     // Maximum ms for single coin passage
#define MULTI_COIN_THRESHOLD  2       // Number of interrupts indicating multiple coins

// ==================== CAMERA SETTINGS ====================
#define CAMERA_FRAME_SIZE     FRAMESIZE_VGA  // 640x480
#define CAMERA_JPEG_QUALITY   10             // JPEG quality (0-63, lower = better)
#define CAMERA_BRIGHTNESS     0              // -2 to 2
#define CAMERA_CONTRAST       0              // -2 to 2

// ==================== LED SETTINGS ====================
#define NUM_CAMERA_LEDS       8       // Number of WS2812B LEDs
#define CAMERA_LED_BRIGHTNESS 128     // 0-255
#define STATUS_LED_BRIGHTNESS 100     // PWM value for status LED

// ==================== SYSTEM STATES ====================
enum CoinMachineState {
    STATE_INIT,
    STATE_WAITING_FOR_COIN,
    STATE_COIN_DETECTED,
    STATE_PROCESSING,
    STATE_PHOTOGRAPHING,
    STATE_REJECTING,
    STATE_ERROR
};

// ==================== STATUS CODES ====================
enum StatusCode {
    STATUS_OK,
    STATUS_MULTIPLE_COINS,
    STATUS_COIN_DURING_PROCESSING,
    STATUS_CAMERA_ERROR,
    STATUS_STORAGE_ERROR,
    STATUS_TIMEOUT_ERROR
};

// ==================== LED COLORS ====================
struct RGBColor {
    uint8_t r, g, b;
};

// Status LED color definitions
const RGBColor LED_READY = {0, 255, 0};        // Green - ready for coin
const RGBColor LED_PROCESSING = {255, 255, 0}; // Yellow - processing coin
const RGBColor LED_BUSY = {255, 0, 0};         // Red - busy/photographing
const RGBColor LED_ERROR = {255, 0, 255};      // Magenta - error
const RGBColor LED_OFF = {0, 0, 0};            // Off

// ==================== FILE STORAGE ====================
#define MAX_IMAGES_STORED     100     // Maximum images before cleanup
#define IMAGE_FILENAME_PREFIX "/coin_"
#define IMAGE_FILENAME_SUFFIX ".jpg"

// ==================== DEBUG SETTINGS ====================
#define DEBUG_ENABLED         true
#define SERIAL_BAUD_RATE      115200

#if DEBUG_ENABLED
    #define DEBUG_PRINT(x)    Serial.print(x)
    #define DEBUG_PRINTLN(x)  Serial.println(x)
#else
    #define DEBUG_PRINT(x)
    #define DEBUG_PRINTLN(x)
#endif

#endif // CONFIG_H 

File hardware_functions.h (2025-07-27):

#ifndef HARDWARE_FUNCTIONS_H
#define HARDWARE_FUNCTIONS_H

#include "config.h"
#include "esp_camera.h"
#include "FS.h"
#include "SPIFFS.h"
#include <ESP32Servo.h>
#include <FastLED.h>

// ==================== GLOBAL HARDWARE OBJECTS ====================
extern Servo trapdoorServo;
extern Servo flipperServo;
extern CRGB cameraLEDs[NUM_CAMERA_LEDS];

// ==================== CAMERA FUNCTIONS ====================
bool initializeCamera() {
    camera_config_t config;
    config.ledc_channel = LEDC_CHANNEL_0;
    config.ledc_timer = LEDC_TIMER_0;
    config.pin_d0 = CAMERA_Y2_PIN;
    config.pin_d1 = CAMERA_Y3_PIN;
    config.pin_d2 = CAMERA_Y4_PIN;
    config.pin_d3 = CAMERA_Y5_PIN;
    config.pin_d4 = CAMERA_Y6_PIN;
    config.pin_d5 = CAMERA_Y7_PIN;
    config.pin_d6 = CAMERA_Y8_PIN;
    config.pin_d7 = CAMERA_Y9_PIN;
    config.pin_xclk = CAMERA_XCLK_PIN;
    config.pin_pclk = CAMERA_PCLK_PIN;
    config.pin_vsync = CAMERA_VSYNC_PIN;
    config.pin_href = CAMERA_HREF_PIN;
    config.pin_sscb_sda = CAMERA_SIOD_PIN;
    config.pin_sscb_scl = CAMERA_SIOC_PIN;
    config.pin_pwdn = -1;
    config.pin_reset = CAMERA_RESET_PIN;
    config.xclk_freq_hz = 20000000;
    config.pixel_format = PIXFORMAT_JPEG;
    
    // Frame size and quality settings
    config.frame_size = CAMERA_FRAME_SIZE;
    config.jpeg_quality = CAMERA_JPEG_QUALITY;
    config.fb_count = 2;
    
    // Initialize camera
    esp_err_t err = esp_camera_init(&config);
    if (err != ESP_OK) {
        DEBUG_PRINTLN("Camera init failed");
        return false;
    }
    
    // Set camera parameters
    sensor_t * s = esp_camera_sensor_get();
    s->set_brightness(s, CAMERA_BRIGHTNESS);
    s->set_contrast(s, CAMERA_CONTRAST);
    
    DEBUG_PRINTLN("Camera initialized successfully");
    return true;
}

bool captureAndSaveImage(const char* filename) {
    // Turn on camera lights
    setCameraLights(true);
    delay(CAMERA_WARMUP_TIME);
    
    // Capture image
    camera_fb_t * fb = esp_camera_fb_get();
    if (!fb) {
        DEBUG_PRINTLN("Camera capture failed");
        setCameraLights(false);
        return false;
    }
    
    // Save to SPIFFS
    File file = SPIFFS.open(filename, FILE_WRITE);
    if (!file) {
        DEBUG_PRINTLN("Failed to open file for writing");
        esp_camera_fb_return(fb);
        setCameraLights(false);
        return false;
    }
    
    file.write(fb->buf, fb->len);
    file.close();
    esp_camera_fb_return(fb);
    
    // Turn off camera lights
    setCameraLights(false);
    
    DEBUG_PRINT("Image saved: ");
    DEBUG_PRINTLN(filename);
    return true;
}

// ==================== SERVO FUNCTIONS ====================
bool initializeServos() {
    trapdoorServo.attach(TRAPDOOR_SERVO_PIN);
    flipperServo.attach(FLIPPER_SERVO_PIN);
    
    // Move to home positions
    trapdoorServo.write(TRAPDOOR_CLOSED);
    flipperServo.write(FLIPPER_HOME);
    
    delay(1000); // Allow servos to reach position
    
    DEBUG_PRINTLN("Servos initialized");
    return true;
}

void setTrapdoorPosition(int angle) {
    trapdoorServo.write(angle);
    DEBUG_PRINT("Trapdoor moved to: ");
    DEBUG_PRINTLN(angle);
}

void setFlipperPosition(int angle) {
    flipperServo.write(angle);
    DEBUG_PRINT("Flipper moved to: ");
    DEBUG_PRINTLN(angle);
}

void openTrapdoor() {
    setTrapdoorPosition(TRAPDOOR_OPEN);
}

void closeTrapdoor() {
    setTrapdoorPosition(TRAPDOOR_CLOSED);
}

void moveFlipperHome() {
    setFlipperPosition(FLIPPER_HOME);
}

void moveFlipperToSide1() {
    setFlipperPosition(FLIPPER_SIDE_1);
}

void moveFlipperToSide2() {
    setFlipperPosition(FLIPPER_SIDE_2);
}

// ==================== LED FUNCTIONS ====================
bool initializeLEDs() {
    // Initialize status LED pins
    pinMode(STATUS_LED_R_PIN, OUTPUT);
    pinMode(STATUS_LED_G_PIN, OUTPUT);
    pinMode(STATUS_LED_B_PIN, OUTPUT);
    
    // Initialize camera LEDs (WS2812B)
    FastLED.addLeds<WS2812B, CAMERA_LIGHTS_PIN, GRB>(cameraLEDs, NUM_CAMERA_LEDS);
    FastLED.setBrightness(CAMERA_LED_BRIGHTNESS);
    
    // Turn off all LEDs initially
    setStatusLED(LED_OFF);
    setCameraLights(false);
    
    DEBUG_PRINTLN("LEDs initialized");
    return true;
}

void setStatusLED(RGBColor color) {
    analogWrite(STATUS_LED_R_PIN, map(color.r, 0, 255, 0, STATUS_LED_BRIGHTNESS));
    analogWrite(STATUS_LED_G_PIN, map(color.g, 0, 255, 0, STATUS_LED_BRIGHTNESS));
    analogWrite(STATUS_LED_B_PIN, map(color.b, 0, 255, 0, STATUS_LED_BRIGHTNESS));
}

void setCameraLights(bool on) {
    if (on) {
        fill_solid(cameraLEDs, NUM_CAMERA_LEDS, CRGB::White);
    } else {
        fill_solid(cameraLEDs, NUM_CAMERA_LEDS, CRGB::Black);
    }
    FastLED.show();
}

void flashCameraLights() {
    setCameraLights(true);
    delay(CAMERA_FLASH_DURATION);
    setCameraLights(false);
}
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

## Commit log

2025-07-26 Create bom
2025-07-27 Update and rename Automated Coin Machine BOM - Sheet1.csv to bom.csv
    [bom.csv]
